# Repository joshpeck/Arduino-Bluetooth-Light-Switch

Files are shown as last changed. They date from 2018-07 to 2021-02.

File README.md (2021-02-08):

# Arduino-Bluetooth-Light-Switch
In this repository are files schematics and instructions on how to make your own bluetooth light switch.

REQUIRED PARTS
1. Arduino Uno w/ power supply of some sort
2. Breadboard
3. 9 Compatable pins (Male to Male)
4. SG90 servo
5. HC-05 Bluetooth Module
6. Access to a a 3D printer
7. Access to a computer
8. A device with bluetooth (what you will use to turn on and off the lights, ex. a smartphone)
9. A 500 ohm and 1000 ohm resistor

INSTRUCTIONS
1. Upload 'BluetoothLightSwitch.ino' onto the Arduino Uno
2. Make sure that you measure your light switch and make any changes to the 3D printing files so that everything fits
3. Print all 3 3D printing components: servo arm, servo holder, and arduino holder
4. Screw on the aruduino holder and servo holder printed components onto the light switch panel
5. Screw the SG90 servo onto the servo holder
6. Place the plastic arm that fits into the servo arm which came with the SG90 servo
7. Place the combination of printed arm and plastic arm onto the servo so that it encloses the light switch
8. Screw on the Arduino onto the Arduino holder
9. Wire the pins according to the provided diagram (WorkingWiring.png)
10. Attach a power supply to the Arduino
11. Connect to the Bluetooth Module on your bluetooth device and send the string "on," or "off," to turn on and off your lights

BLUETOOTH MODULE PROGRAMMING
1. Disconnect the module from the arduino
2. Upload an empty file to the arduino
3. Switch the RX and TX pins so that the module is wired according to ATModeWiring.png
4. Reconnect the bluetooth module
5. Power the arduino via USB on a computer with Arduino Sketch installed while holding down the module button
6. After 2 seconds, you'll notice the blue light on the module blinking every 2 seconds, this means the module is in programming mode
7. Open the serial monitor in Arduino Sketch and set the bottom right boxes to 'Both NL & CR' and '9600 baud'
8. Type the command 'AT' twice, and if an 'OK' appears, then you can type your programming commands

ADDITIONAL NOTES
- The app I use for this project is "Serial Bluetooth Terminal" in the Play Store. If you use this, ensure that the Receive Newline is 'CR+LF' and the Send Newline is 'None'
- When uploading a .ino file to the arduino, make sure the servo and bluetooth module are disconnected
- This project only works with traditional 'toggle' light switches.
- Due to the nature of the bluetooth module I used, a voltage divider was needed (cutting 5V to 3.3V). This uses additional energy on standby than just the Arduino Uno alone.

[<3 AlexeyY]

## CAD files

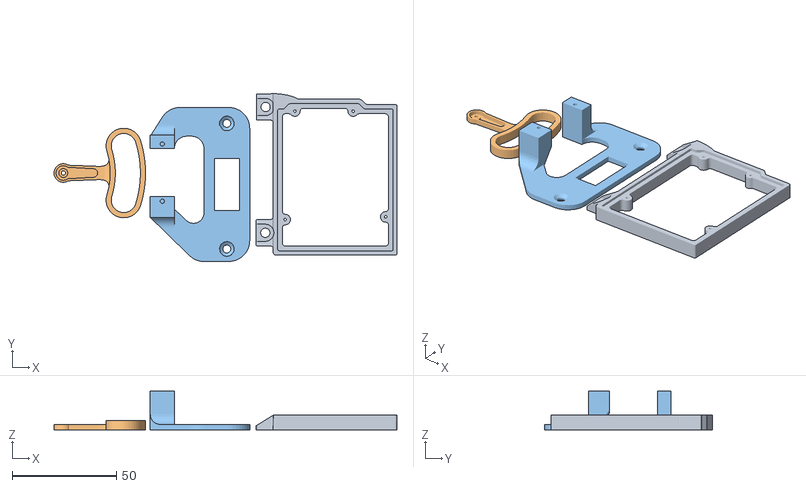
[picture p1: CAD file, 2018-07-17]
What to print/All Three Closer/tinker.obj
164.7 x 80.7 x 18.5

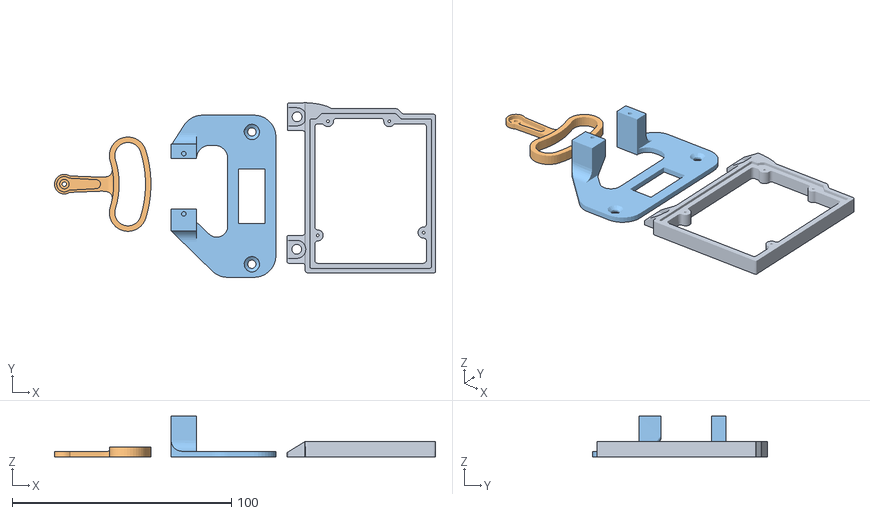
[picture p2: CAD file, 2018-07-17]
What to print/All Three/tinker.obj
173.7 x 79.7 x 18.5

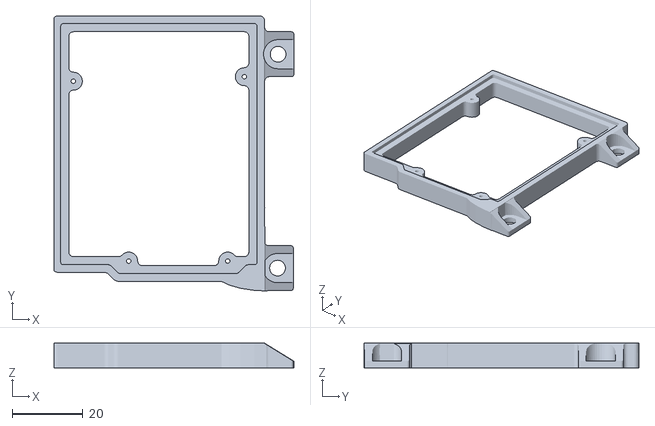
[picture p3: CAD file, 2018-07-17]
What to print/Arduino Holder(right side port down).stl
67.7 x 77.7 x 7.00

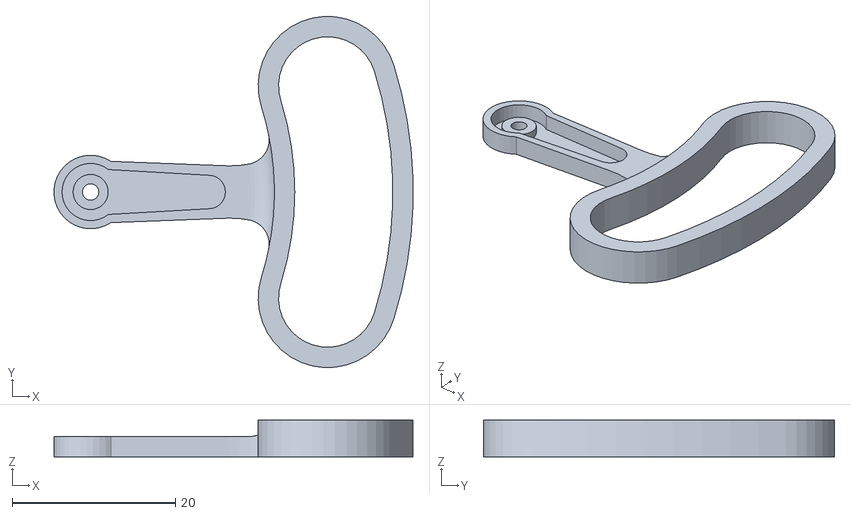
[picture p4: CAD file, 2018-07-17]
What to print/Servo Arm/tinker.obj
44.0 x 43.0 x 4.50

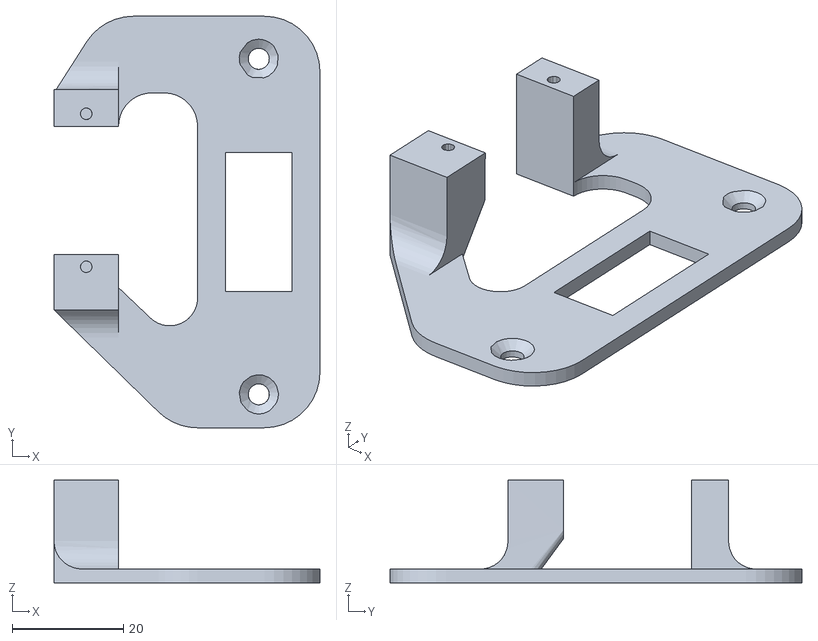
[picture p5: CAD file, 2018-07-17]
What to print/Servo Holder/tinker.obj
47.8 x 74.0 x 18.5

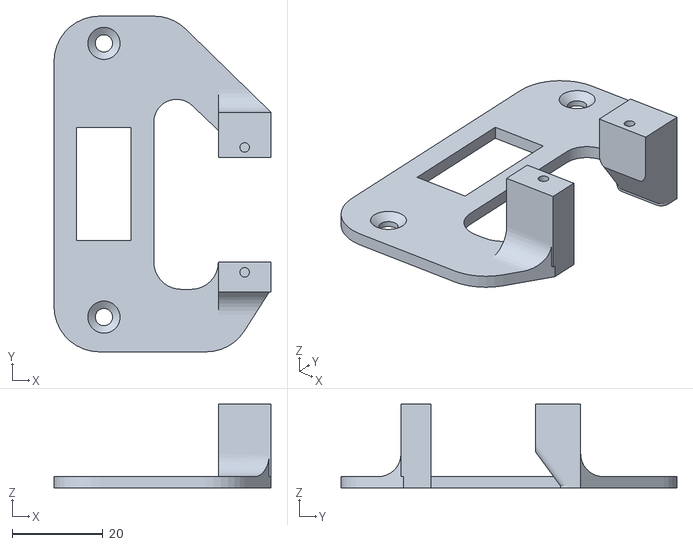
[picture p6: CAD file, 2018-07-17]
What to print/Servo Holder.STL
47.8 x 74.0 x 18.5

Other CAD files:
What to print/Arduino Holder/tinker.obj
What to print/Servo Arm.STL
What to print/All Three Closer.stl
What to print/All Three.stl

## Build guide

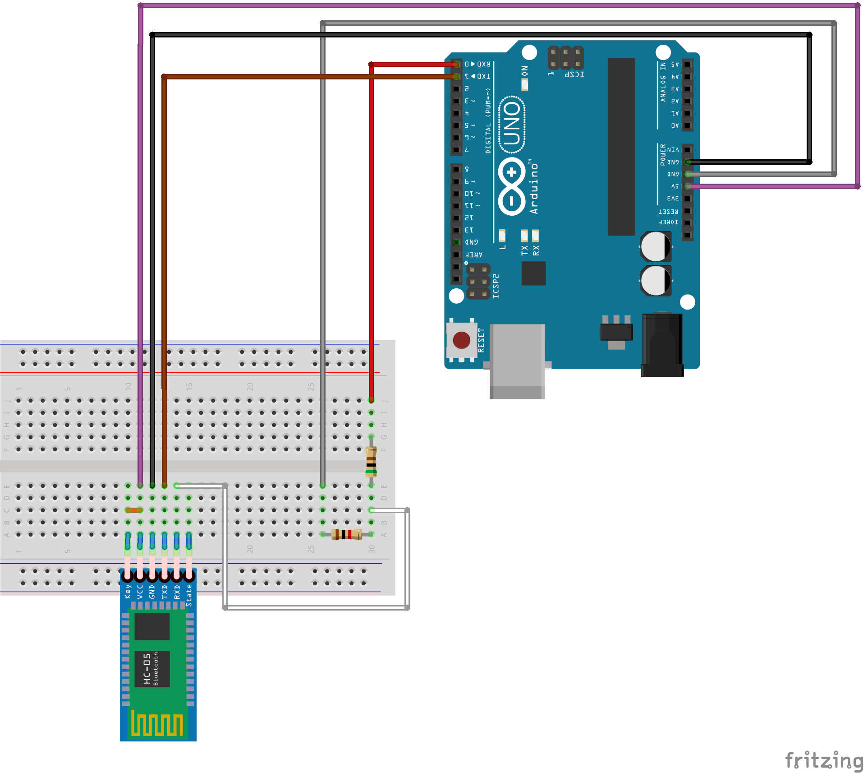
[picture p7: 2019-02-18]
ATModeWiring.png

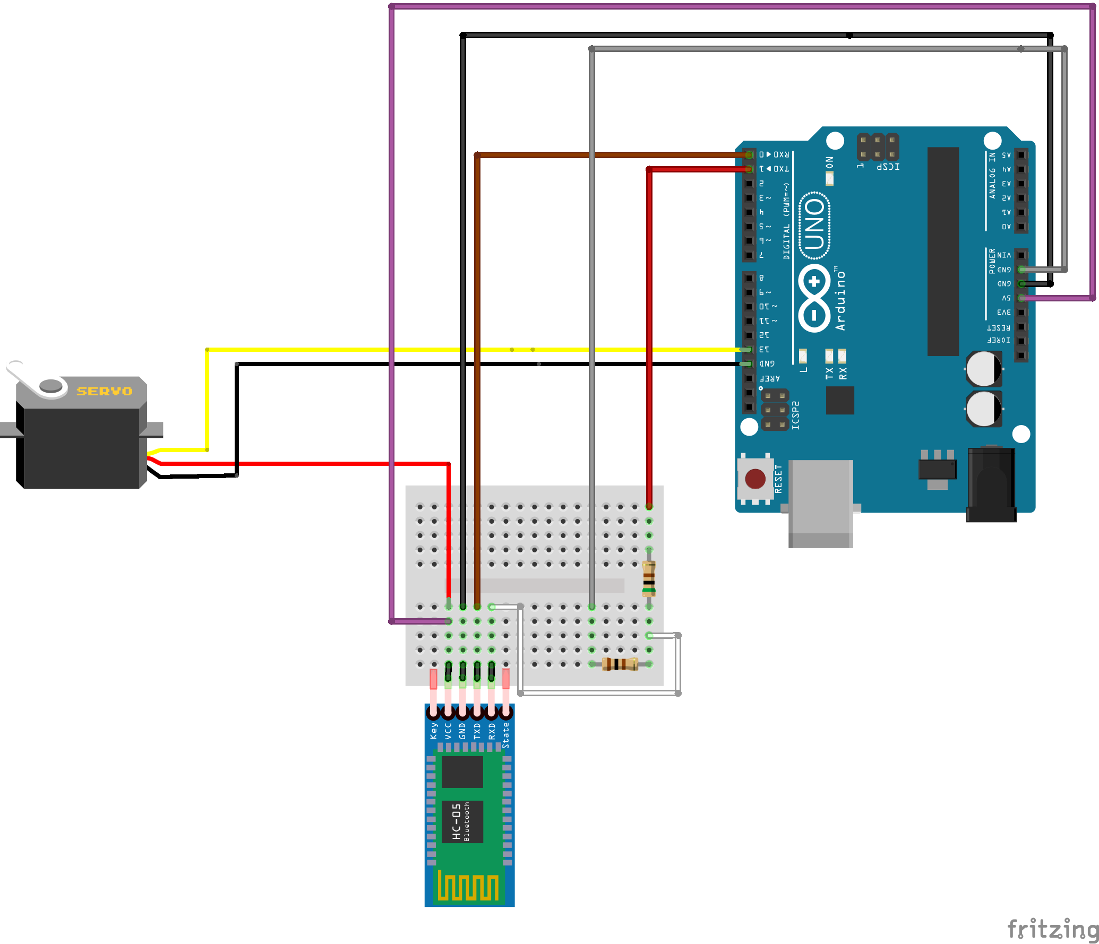
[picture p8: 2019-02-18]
WorkingWiring.png

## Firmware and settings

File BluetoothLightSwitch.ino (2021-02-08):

#include <Servo.h>

Servo servo;

#define COMMAND_SIZE 21 // Size of command buffer
#define PRINT_SIZE 101 // Size of command buffer

//Variables
int defCenter = 42;
int defUp = 13;
int defDown = 84;

int center = defCenter;
int up = defUp;
int down = defDown;

char buf1[COMMAND_SIZE];  // Allow up to 21 character commands
char buf2[PRINT_SIZE];    // Allow up to 101 character print statements
int chars;                // Keep track of how many characters we have used before a ','

void setup() {
  // put your setup code here, to run once:
  Serial.begin(9600); //BAUD rate
  
  chars = 0;
  memset(buf1, 0, COMMAND_SIZE);
  memset(buf2, 0, PRINT_SIZE);

  pinMode(13, OUTPUT);

  servo.attach(13);
  servo.write(center);
  servo.detach();

  resetVars();
}

void loop() {
  // put your main code here, to run repeatedly:
  digitalWrite(13, LOW);

  if (Serial.available() > 0) {
    if(chars == 0)
      Serial.println("");
    char c = Serial.read();
    buf1[chars] = c;
    chars++;
    //memset(buf2, 0, PRINT_SIZE);
    //sprintf(buf2, "Current command line is: \"%s\" with latest char \"%c\"", buf1, c);
    //Serial.println(buf2);
    if (c == ',') {
      if (!strncmp(buf1,"on",2)) {
        Serial.println("Turning on");
        servo.attach(13);
        servo.write(up);
        delay (1500);
        servo.write(center);
        delay (500);
        digitalWrite(13, LOW);
        servo.detach();
      }
      else if (!strncmp(buf1,"off",3)) {
        Serial.println("Turning off");
        servo.attach(13);
        servo.write(down);
        delay (1500);
        servo.write(center);
        delay (500);
        digitalWrite(13, LOW);
        servo.detach();
      }
      else if (!strncmp(buf1,"vars",4)) {
        printVars();
      }
      else if (!strncmp(buf1,"reset",5)) {
        Serial.println("Reset variables");
        resetVars();
      }
      else if (!strncmp(buf1,"commands",8)) {
        printCommands();
      }
      else if (strlen(buf1) >= 8 && !strncmp(buf1,"center",6)) {
        int angle = atoi(buf1+7);
        center = angle;
        memset(buf2, 0, PRINT_SIZE);
        sprintf(buf2, "Set \"center\" to %d", angle);
        Serial.println(buf2);
      }
      else if (strlen(buf1) >= 4 && !strncmp(buf1,"up",2)) {
        int angle = atoi(buf1+3);
        up = angle;
        memset(buf2, 0, PRINT_SIZE);
        sprintf(buf2, "Set \"up\" to %d", angle);
        Serial.println(buf2);
      }
      else if (strlen(buf1) >= 6 && !strncmp(buf1,"down",4)) {
        int angle = atoi(buf1+5);
        down = angle;
        memset(buf2, 0, PRINT_SIZE);
        sprintf(buf2, "Set \"down\" to %d", angle);
        Serial.println(buf2);
      }
      else {
        printHelp();
      }
      chars = 0;
      memset(buf1, 0, COMMAND_SIZE);
    }
  }
  delay(50);
}

void resetVars() {
  center = defCenter;
  up = defUp;
  down = defDown;
}

void printHelp() {
  Serial.println("");
  Serial.println("Enter \'vars\' to see current variable values");
  Serial.println("Enter \'commands\' to see commands");
  Serial.println("Enter \'help\' to see this page again");
}

void printVars() {
  Serial.println("");
  Serial.println("Default center angle: 42");
  Serial.println("Default up angle: 13");
  Serial.println("Default down angle: 84");
  Serial.println("Current center angle: " + String(center) + "");
  Serial.println("Current up angle: " + String(up) + "");
  Serial.println("Current down angle: " + String(down) + "");
}

void printCommands() {
  Serial.println("");
  Serial.println("To change angle, enter: \'variable\'");
  Serial.println("such as \'center\', \'up\', or \'down\'");
  Serial.println("and the new angle");
  Serial.println("Enter \'reset\' to set variables to default");
}
